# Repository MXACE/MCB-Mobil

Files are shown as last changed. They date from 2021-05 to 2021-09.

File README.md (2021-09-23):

# MCB-Mobil
A selfmade RC car with mecanuum wheels.

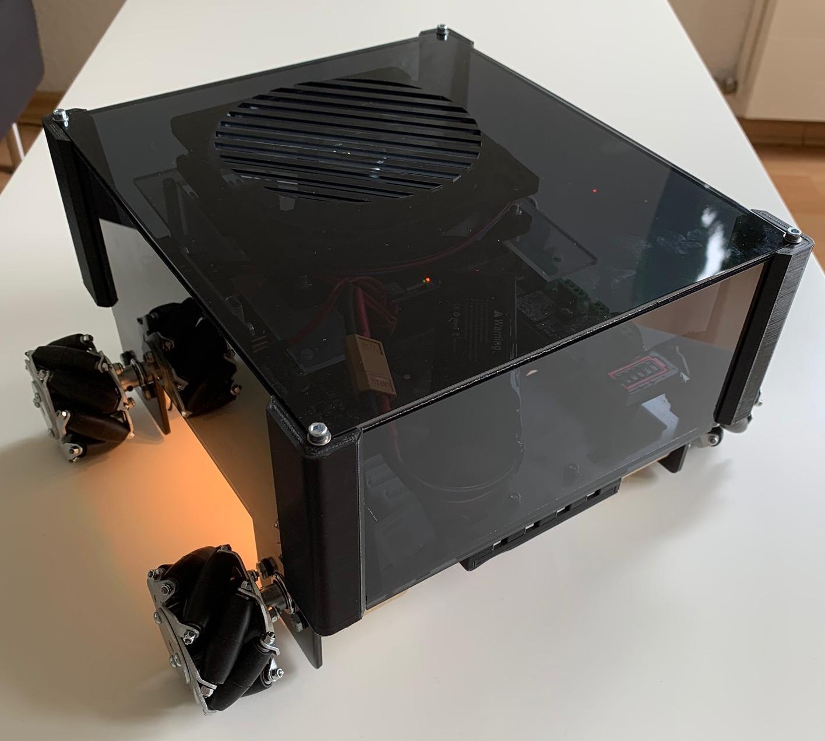
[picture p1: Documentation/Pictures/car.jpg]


## Important Notes
The Software written for the STM microcontroller is for the [STM32Workbench](https://www.st.com/en/development-tools/sw4stm32.html) IDE.
The Software written for the Arduino is made in [Arduino](https://www.arduino.cc/en/software)

The controller is on version 2.0. The old files of version 1.0 are not on this github.
See "Controller Changelog" or the documentation below for more information.

[First Documentation v1.0](https://github.com/MXACE/MCB-Mobil/tree/master/Documentation/MCB_Mobil_Doku_LarsPeter_MarcoStauber.pdf)

[Second Documentation (Controller v2.0)](https://github.com/MXACE/MCB-Mobil/tree/master/Documentation/Doku_controller.pdf)

## Controller Changelog
v2.0
- Added BMG250 Sensor.
- Removed OLED Connector.
- Added OLED Screen COM connector.
- Changed microcontroller from STM32F107VC to STM32F405RGT6.
- Removed connection for Lora Breakout Board.
- Added RN2483 Lora Module directly on PCB.
- Replaced 20pin JTAG conntector with 5 Pin SWD connector and TagConnect pads.
- Removed onboard STLINK and it's USB Connector.
- Added Powerswitch between Battery and USB.
- Several layout changes.

## Important Files:

Schematics of the Car, Controller and the Lora Breakoutboard can be found [here](https://github.com/MXACE/MCB-Mobil/tree/master/All_Schematics)

### Car:
- [PCB Files](https://github.com/MXACE/MCB-Mobil/tree/master/Car/CAD/v1.0/Chassisv1.0)
- [3D Printed Casing Parts (Scheinwerfer & Plexiglashalter)](https://github.com/MXACE/MCB-Mobil/tree/master/Car/3d%20modell/3dprint)
- [Software for STM32F107](https://github.com/MXACE/MCB-Mobil/tree/master/Car/SW)
- [Software for Arduino Nano](https://github.com/MXACE/MCB-Mobil/tree/master/Car/SW_ARD)
- [BOM](https://github.com/MXACE/MCB-Mobil/tree/master/Car/Assembly)

### Controller:
- [PCB Files](https://github.com/MXACE/MCB-Mobil/tree/master/Controller/PCB)
- [3D Printed Casing Parts](https://github.com/MXACE/MCB-Mobil/tree/master/Controller/Assembly)
- [Software for STM32F405](https://github.com/MXACE/MCB-Mobil/tree/master/Controller/SW)
- [BOM](https://github.com/MXACE/MCB-Mobil/tree/master/Controller/BOM)

### RN2483 Lora Breakout Module
- [PCB Files](https://github.com/MXACE/MCB-Mobil/tree/master/Funk/CAD/v1.0/PCB_Project)
- [BOM](https://github.com/MXACE/MCB-Mobil/tree/master/Funk/Assembly)

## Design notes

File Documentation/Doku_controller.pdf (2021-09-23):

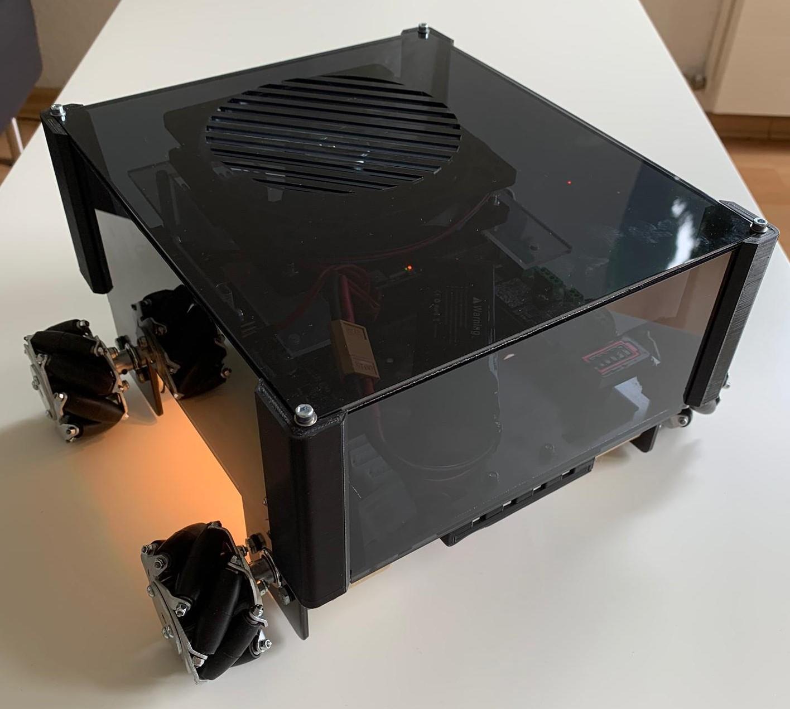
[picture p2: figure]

# MCB Mobil

Marco Stauber

Ben17A

## Inhaltsverzeichnis

## Abstract

Die erste Version des Kontrollers funktionierte nicht mehr und hatte viele Designfehler. Am einfachsten ging es mit einem neuem Design und einem neuem Print.
Das Ziel war es das bereits begonnene Projekt „MCB Mobil“ fertig zu stellen und ein zweites Fahrzeug für Herrn Malacarne zusammen zu bauen.

## Zusätzliche Infos

Alle Dateien für das Projekt können auf dem folgenden GitHub gefunden werden:

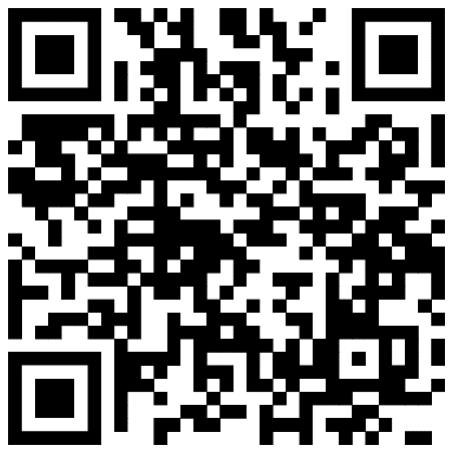
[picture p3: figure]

https://github.com/MXACE/MCB-Mobil

## Änderungen

Anstelle eines RN2483-Breakoutboard das ich selbst gemacht habe, befindet sich direkt ein solches Modul auf dem Print. Dieses ist zuständig für die Kommunikation mit dem Fahrzeug. Zur Sicherheit habe ich den Footprint des Breakoutboards trotzdem hinzugefügt, falls das Modul auf dem PCB nicht funktioniert.

Da das mit dem Bootloader nicht geklappt hat, konnte ich ihn ganz weg lassen. Somit sparte ich nicht nur Platz, sondern auch noch Geld und viele Bauteile wie ein zweiter Mikrokontroller oder ein USB Anschluss.

Die Joysticks befinden sich nun auf der gleichen Höhe vom Print. Ein Fehler den ich gemacht habe war, dass ich den linken Joystick nicht um 45° gedreht habe. Dies würde es vereinfachen das Fahrzeug zu steuern, da es mit den Mecannum Rädern andere Fahrtrichtungen hat.

Diese Räder besitzen Rollen die im 45° Winkel montiert wurden. Somit verändert es die Fahrtrichtung.
In der linken Abbildung sieht man die Fahrtrichtungen mit herkömmlichen Rädern.
In der rechten Abbildung sieht man die orangen Kräftevektoren der einzelnen Räder. Kombiniert man diese beliebig, kann man mit dem Fahrzeug in alle Richtungen fahren.

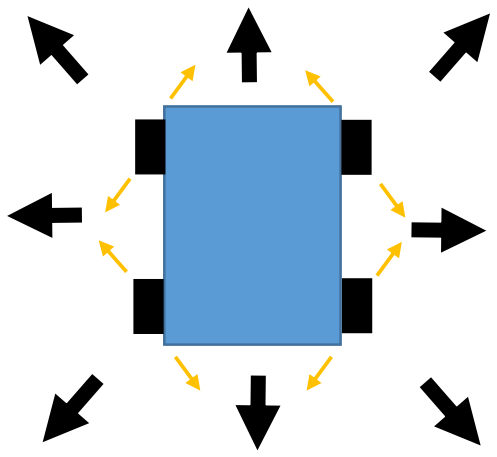
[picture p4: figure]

Neben den zusätzlichen Debug-LEDs gibt jetzt noch eine Schaltung für die Speisung. Ein PMOS stellt die Speisung der Batterie hochohmig, sobald sich eine Spannung am USB-Port befindet. Dies soll verhindern, dass die Batterie sich schnell entlädt.

Ein Achsensensor, der BMG250 von Bosch, sollte eine zweite Möglichkeit sein um das Fahrzeug zu steuern, indem man den Kontroller in die jeweilige Richtung kippt.

## Funktionen

Um das eine Problem mit den Joystick zu beheben, musst ich nur die XY Koordinaten davon um 45° drehen. Durch eine Anleitung auf YouTube konnte ich einfach herausfinden wie es funktioniert.

∝ = 45° → cos(∝) = sin(∝) =

√2
2

= √0.5 ≈ 0.707

x45 = x × cos(∝) − y × sin(∝) = x × √0.5 − y × √0.5

y45 = x × cos(∝) + y × sin(∝) = x × √0.5 + y × √0.5

Da der Sinus und der Cosinus aus der Math.h Library den ganzen Speicher füllen würden nahm ich anstelle von cos(45°) und sin(45°), 0.707 für die Rechnung.

Da mir die Zeit fehlte kam ich nicht weit beim Kommunikationsprotokoll zwischen dem Fahrzeug und dem Kontroller. Also war die Lösung: eine Kommunikation nur in eine Richtung. Der Kontroller schickt alle 0.5 Sekunden eine Nachricht mit allen Joystick Werten. Im Fall das eine Nachricht ausfallen sollte und das Fahrzeug 0.5 Sekunden lang keine Daten bekommt, bleibt es stehen. Der Kontroller muss daher einfach neugestartet werden. Das Fahrzeug wartet ein paar Sekunden und geht dann wieder in RX Modus. Gleichzeitig sieht man das an den LEDS um das Fahrzeug.

Der Bildschirm ist nun ein wenig überflüssig. Dieser zeigt nur noch an wann der Kontroller bereit ist für den Start und die Steuerung des Scheinwerfers.

## Probleme

Der Achsensensor hat mich sehr viel Zeit gekostet. Das Hautproblem war die Kommunikation mit dem Chip. Designt habe ich ihn für SPI. Nach nahezu endlosen neuprogrammieren und neu löten wurde es immer noch nichts. Als ich es mit einem STM Discovery und der Breakout Version des BMG250 über I2C versuchte ging es. Auf dem Kontroller wiederrum nicht, also hab ich das ganze sein gelassen.

Bei dem Aufsetzten der Unidirektionalen Kommunikation gab es auch ein Paar Fehler die aber auf der Priorität der Interrupts zurückzuführen war.

## Fazit

Nun im letzten Semester konnte ich mein Fahrzeug endlich fertig stellen. Das mit dem Achsensensor fand ich eine coole Idee, wurde aber nur anstrengend und hat mich zu viel Zeit gekostet. Für das ich gesamthaft Eineinhalb Jahre an diesem Projekt dran war, hat es mir sehr viel Freude bereitet. Es war nicht immer einfach daran zu arbeiten, da viele Abschlussprüfungen und sonst noch welche Dinge dazwischen kamen.

Das Fahrzeug fährt jetzt immerhin und es funktioniert grösstenteils. Es gäbe noch ein paar Verbesserungen, wie zum Beispiel eine Akkuschutzschaltung oder einen kleineren Print, die man bei der nächsten Version machen könnte.

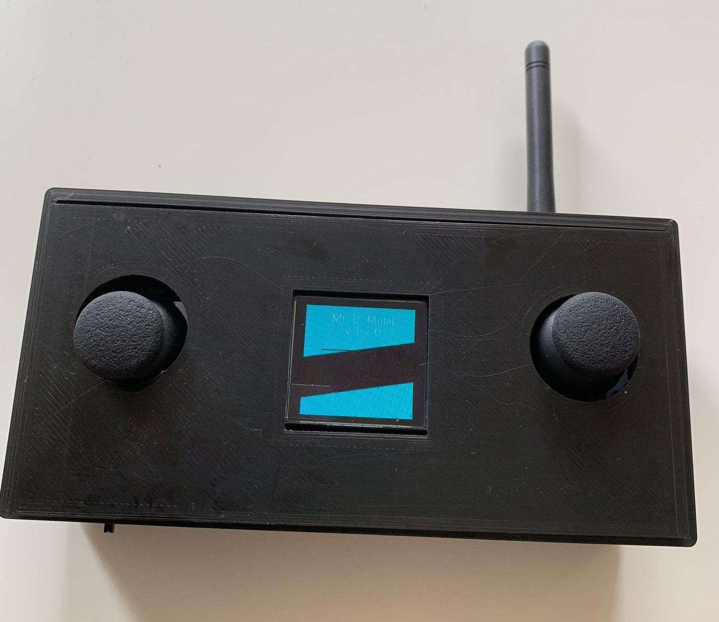
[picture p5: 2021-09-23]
Documentation/Pictures/Controller.jpg

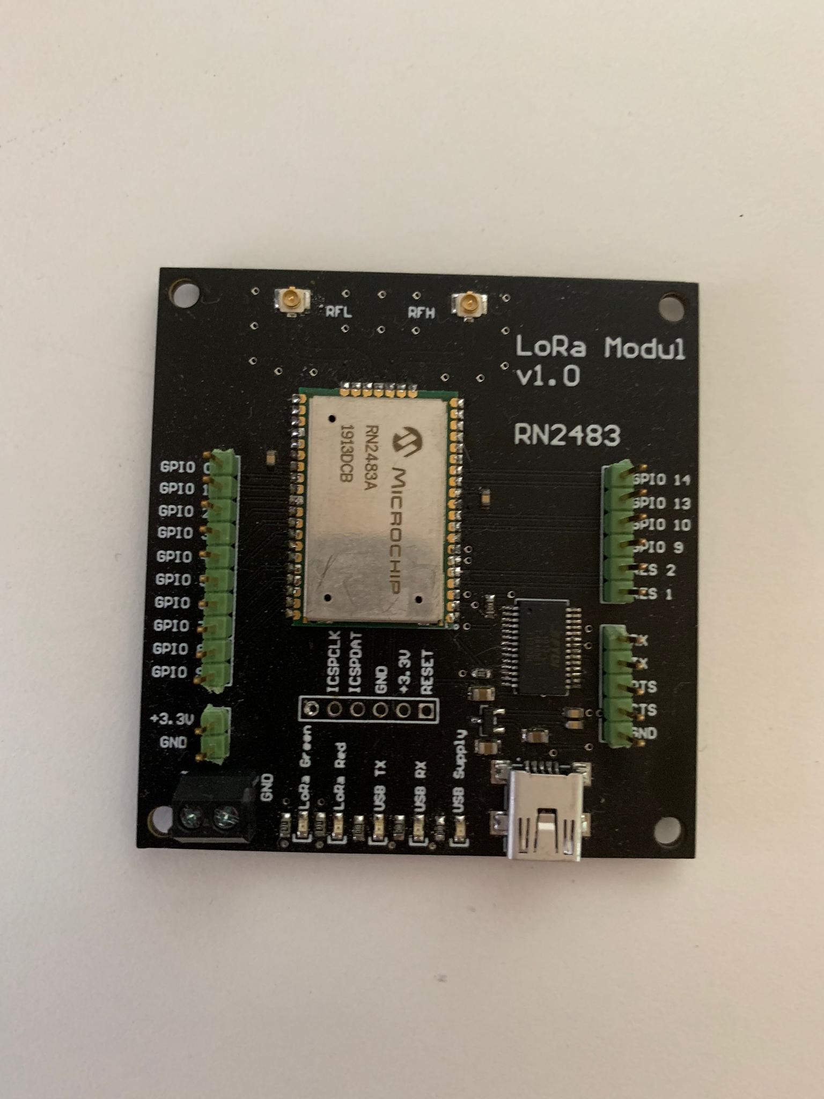
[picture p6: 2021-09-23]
Documentation/Pictures/LoraBreakout.jpg

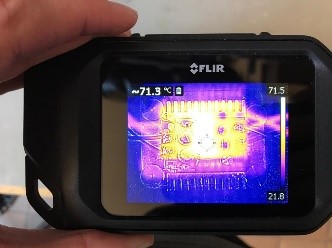
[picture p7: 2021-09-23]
Documentation/Pictures/Temperature_DCDC.jpg

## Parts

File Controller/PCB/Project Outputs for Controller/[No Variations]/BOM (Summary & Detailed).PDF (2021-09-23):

Designator | Description | Comment | Footprint | Quantity | Ma nuf No act te ure r | Su Su Su ppl ppl ppl ier ier ier 1 2 3 | Su Su Su ppl ppl ppl ier ier ier 1 2 3 Par Par Par t t t Nu Nu Nu mb mb mb er er er | Ma nuf act SMS-ure r Lab Par Part t Num ber Nu mb er | Value | Center-X(mm) | Center-Y(mm) | Layer | Assembly Technology | Rotation
| | LoRa Modul | LoRA | | 1 | | | | | 73.51 | 30.811 | Bottom | | 270
C1 | capacitor | 22 pF | CAP_0603i_1608m -N | | 1 | | | | | 90.369 | 21.535 | Top | | 180
C2 | capacitor | 22 pF | CAP_0603i_1608m -N | | 1 | | | | | 93.8 | 18.682 | Top | | 270
C3 | capacitor | 100nF | CAP_0603i_1608m -N | | 1 | | | | | 126.3 | 10.6 | Top | | 0
C4 | capacitor | 100nF | CAP_0603i_1608m -N | | 1 | | | | | 94.226 | 13.684 | Top | | 0
C5 | | Capacitor_0805 | 10uF_0805_Chip2Pi nSM127P600-8N | | 1 | | | | | 131.35 | 56.691 | Top | | 270
C6 | capacitor | 1 uF | CAP_0805i_2012m -N | | 1 | | | | | 80.2 | 59.882 | Top | | 90
C7 | | Capacitor_0603 | C_0603_Chip2PinS M127P600-8N | | 1 | | | | | 111.35 | 64.35 | Top | | 180
C8 | capacitor | 1 uF | CAP_0805i_2012m -N | | 1 | | | | | 70.9 | 60.103 | Top | | 270
C9 | | Capacitor_0603 | C_0603_Chip2PinS M127P600-8N | | 1 | | | | | 118.2 | 56.7 | Top | | 90
C10 | | Capacitor_0603 | C_0603_Chip2PinS M127P600-8N | | 1 | | | | | 59 | 47.585 | Top | | 180
C11 | | Capacitor_0603 | C_0603_Chip2PinS M127P600-8N | | 1 | | | | | 119.9 | 56.7 | Top | | 90
C12 | | Capacitor_0603 | C_0603_Chip2PinS M127P600-8N | | 1 | | | | | 133.35 | 56.691 | Top | | 90
C13 | | Capacitor_0603 | C_0603_Chip2PinS M127P600-8N | | 1 | | | | | 121.55 | 56.7 | Top | | 90
C14 | capacitor | 100nF | CAP_0603i_1608m -L | | 1 | | | | | 58.558 | 54.86 | Top | | 180
C15 | capacitor | 10 uF | CAP_0805i_2012m -N | | 1 | | | | | 55.568 | 61.238 | Top | | 270
C16 | capacitor | 100nF | CAP_0603i_1608m -L | | 1 | | | | | 51.653 | 58.8 | Top | | 270
C17 | capacitor | 22 pF | CAP_0603i_1608m -N | | 1 | | | | | 82.362 | 36.166 | Top | | 90
C18 | capacitor | 0.1 uF | CAP_0603i_1608m -N | | 1 | | | | | 81.583 | 31.445 | Top | | 270
C19 | capacitor | 0.1 uF | CAP_0603i_1608m -N | | 1 | | | | | 70.42 | 46.456 | Top | | 180
C20 | capacitor | 22 pF | CAP_0603i_1608m -N | | 1 | | | | | 78.658 | 31.453 | Top | | 90
C21 | capacitor | 0.1 uF | CAP_0603i_1608m -N | | 1 | | | | | 70 | 25.306 | Top | | 0
C22 | capacitor | 0.1 uF | CAP_0603i_1608m -N | | 1 | | | | | 51.653 | 28.756 | Top | | 90
C23 | capacitor | 0.1 uF | CAP_0603i_1608m -N | | 1 | | | | | 59 | 45.85 | Top | | 180
C24 | capacitor | 0.1 uF | CAP_0603i_1608m -N | | 1 | | | | | 79.63 | 39.112 | Top | | 0
C25 | capacitor | 0.1 uF | CAP_0603i_1608m -N | | 1 | | | | | 78 | 40.624 | Top | | 180
C26 | capacitor | 0.1 uF | CAP_0603i_1608m -N | | 1 | | | | | 78 | 42.306 | Top | | 0
C27 | capacitor | 10 uF | CAP_0805i_2012m -N | | 1 | | | | | 86.908 | 49.15 | Top | | 180
CR1 | | STM32F103C8T6 | LQFP-48 | | 1 | | | | STM32F 103C8T 6 | 103.582 | 16.044 | Top | | 0
D1 | LED; SMD; 0603; grün; 35mcd; 1.6x0.8x0.55mm; 130Â°; 2Ã·2.V; 20mA | Grün | *0603 | | 1 | | | | | 120.963 | 2.6 | Top | | 90
D2 | LED; SMD; 0603; orange; 45-90mcd; 1.6x0.8x0.55mm; 130Â°; 2Ã·2.4V; 20mA | Orange | *0603 | | 1 | | | | | 118.882 | 2.6 | Top | | 90
D3 | LED; SMD; 0603; grün; 35mcd; 1.6x0.8x0.55mm; 130Â°; 2Ã·2.V; 20mA | Grün | *0603 | | 1 | | | | | 80.2 | 67.704 | Top | | 270
D4 | | BAT54T1G | BAT54T1G_SODFL3 71X135-2N | | 1 | | | | | 105.985 | 61.975 | Top | | 180
D5 | LED; SMD; 0603; grün; 35mcd; 1.6x0.8x0.55mm; 130Â°; 2Ã·2.V; 20mA | Grün | *0603 | | 1 | | | | | 51.051 | 66.882 | Top | | 270
D6 | LED; SMD; 0603; orange; 45-90mcd; 1.6x0.8x0.55mm; 130Â°; 2Ã·2.4V; 20mA | Orange | *0603 | | 1 | | | | | 53.178 | 66.882 | Top | | 270
D7 | | 1N4148 | 1N4148_SODFL127P 600-8N | | 1 | | | | | 127.35 | 56.691 | Top | | 90
D8 | | 1N4148 | 1N4148_SODFL127P 600-8N | | 1 | | | | | 125.35 | 56.691 | Top | | 270
D9 | LED; SMD; 0603; grün; 35mcd; 1.6x0.8x0.55mm; 130Â°; 2Ã·2.V; 20mA | Grün | *0603 | | 1 | | | | | 24.07 | 14.9 | Top | | 270
F1 | | Fuse | FUSE-3586KTR | | 1 | | | | | 19.02 | 8.95 | Top | | 0
IC1 | USB-to-UART 1-CH 256byte FIFO 5V 28-Pin SSOP Tube | FT232RL-TUBE | *SSOP28-LD | | 1 | | | | | 50.678 | 50.193 | Top | | 0
J1 | Mini AB, USB 2.0, 1 A, Right Angle, Surface Mount _SMT_, USB Receptacle | UJ2-MABH-4-SMT | *CUI_UJ2-MABH-4-SMT_UJ2-MABH-4-SMT(Primary) | | 1 | | | | | 129.3 | 5.16 | Top | | 0
J2 | Mini AB, USB 2.0, 1 A, Right Angle, Surface Mount _SMT_, USB Receptacle | UJ2-MABH-4-SMT | *CUI_UJ2-MABH-4-SMT_UJ2-MABH-4-SMT(Primary) | | 1 | | | | | 63.48 | 64.87 | Top | | 180
J3 | | Joystick | Joystick | | 1 | | | | | 21.99 | 39.004 | Top | | 0
J4 | | Joystick | Joystick | | 1 | | | | | 128.01 | 39 | Top | | 180
L1 | | Inductor_0805 | 0805_INDC2012X12 N | | 1 | | | | | 103.35 | 64.975 | Top | | 270
L2 | Inductor | Inductor | Murata Inductor 2900 sch | | 1 | | | | | 79.923 | 46.85 | Top | | 90
P1 | Header, 4-Pin | Header 4 | HDR1X4 | | 1 | | | | | 114.421 | 21.533 | Top | | 180
P2 | Header, 5-Pin | SWIM | HDR1X5 | | 1 | | | | | 102.042 | 32.254 | Top | | 0
P3 | Header, 5-Pin | SWD | HDR1X5 | | 1 | | | | | 122.582 | 15.895 | Top | | 90
P6 | Single Pad or Testpoint | ON-OFF | MotConnector | | 1 | | | | | 14.8 | 2.9 | Top | | 0
P7 | Connector; IDC, Male Header, Thru-Hole; 20 Position; Vertical; Pitch 2.54mm; B | IDC-20 | IDC-20 | | 1 | | | | | 24.7 | 62.96 | Top | | 0
P8 | Single Pad or Testpoint | Batterie | MotConnector | | 1 | | | | | 26.07 | 2.9 | Top | | 0
R1 | Resistor | 1000 | RES_0603i_1608m -N | | 1 | | | | | 120.963 | 6.6 | Top | | 90
R2 | Resistor | 1000 | RES_0603i_1608m -N | | 1 | | | | | 118.882 | 6.6 | Top | | 270
R3 | Resistor | 100K | RES_0603i_1608m -N | | 1 | | | | | 96.9 | 10.4 | Top | | 270
R4 | Resistor | 100K | RES_0603i_1608m -N | | 1 | | | | | 98.576 | 10.374 | Top | | 90
R5 | Resistor | 390 | RES_0603i_1608m -N | | 1 | | | | | 90.369 | 15.657 | Top | | 0
R6 | Resistor | 10K | RES_0603i_1608m -N | | 1 | | | | | 102.218 | 34.59 | Top | | 0
R7 | Resistor | 10K | RES_0603i_1608m -N | | 1 | | | | | 104.332 | 8.454 | Top | | 90
R8 | Resistor | 10K | RES_0603i_1608m -N | | 1 | | | | | 94.226 | 15.397 | Top | | 180
R9 | Resistor | 220 | RES_0603i_1608m -N | | 1 | | | | | 101.888 | 24.814 | Top | | 270
R10 | Resistor | 220 | RES_0603i_1608m -N | | 1 | | | | | 104.83 | 24.814 | Top | | 270
R11 | Resistor | 220 | RES_0603i_1608m -N | | 1 | | | | | 99.463 | 28.544 | Top | | 270
R12 | Resistor | 100 | RES_0603i_1608m -N | | 1 | | | | | 114.453 | 13.355 | Top | | 180
R13 | Resistor | 22 | RES_0603i_1608m -N | | 1 | | | | | 101.888 | 28.564 | Top | | 270
R14 | Resistor | 22 | RES_0603i_1608m -N | | 1 | | | | | 104.776 | 28.56 | Top | | 270
R15 | Resistor | 22 | RES_0603i_1608m -N | | 1 | | | | | 118.103 | 13.355 | Top | | 180
R16 | Resistor | 22 | RES_0603i_1608m -N | | 1 | | | | | 118.103 | 15.895 | Top | | 180
R17 | Resistor | 22 | RES_0603i_1608m -N | | 1 | | | | | 118.103 | 18.435 | Top | | 180
R18 | Resistor | 1K | RES_0603i_1608m -N | | 1 | | | | | 80.2 | 63.742 | Top | | 90
R19 | | Resistor_0603 | R_0603_Chip2PinS M127P600-8N | | 1 | | | | | 111.35 | 62.735 | Top | | 0
R20 | | Resistor_0603 | R_0603_Chip2PinS M127P600-8N | | 1 | | | | | 111.35 | 65.925 | Top | | 180
R21 | Resistor | 1000 | RES_0603i_1608m -N | | 1 | | | | | 51.051 | 62.882 | Top | | 90
R22 | Resistor | 1000 | RES_0603i_1608m -N | | 1 | | | | | 53.178 | 62.882 | Top | | 90
R23 | Resistor | 1K | RES_0603i_1608m -N | | 1 | | | | | 46.453 | 43.851 | Top | | 270
R24 | Resistor | 1K | RES_0603i_1608m -N | | 1 | | | | | 49.079 | 43.851 | Top | | 270
R25 | | Resistor_0603 | R_0603_Chip2PinS M127P600-8N | | 1 | | | | | 129.35 | 56.691 | Top | | 90
R26 | | Resistor_0603 | R_0603_Chip2PinS M127P600-8N | | 1 | | | | | 123.2 | 56.7 | Top | | 90
R27 | Resistor | Res | RES_0603i_1608m -N | | 1 | | | | | 76.11 | 31.598 | Top | | 90
R28 | Resistor | 390 | RES_0603i_1608m -N | | 1 | | | | | 76.86 | 36.206 | Top | | 270
R29 | Resistor | 10K | RES_0603i_1608m -N | | 1 | | | | | 20.8 | 14.9 | Top | | 90
R30 | Resistor | 10K | RES_0603i_1608m -N | | 1 | | | | | 28.51 | 55.925 | Top | | 270
R31 | Resistor | 10K | RES_0603i_1608m -N | | 1 | | | | | 25.97 | 55.925 | Top | | 270
R32 | Resistor | 10K | RES_0603i_1608m -N | | 1 | | | | | 21 | 55.925 | Top | | 270
R33 | Resistor | 10K | RES_0603i_1608m -N | | 1 | | | | | 56.9 | 26.208 | Top | | 90
R34 | Resistor | 10K | RES_0603i_1608m -N | | 1 | | | | | 18.4 | 55.925 | Top | | 270
R35 | Resistor | 10K | RES_0603i_1608m -N | | 1 | | | | | 33.59 | 55.925 | Top | | 90
R36 | Resistor | 10K | RES_0603i_1608m -N | | 1 | | | | | 15.9 | 55.925 | Top | | 270
R37 | Resistor | 10K | RES_0603i_1608m -N | | 1 | | | | | 36.13 | 55.925 | Top | | 90
S1 | Switch | SW PB | B3SL-1002P | | 1 | | | | | 78.86 | 26.218 | Top | | 180
U1 | | OLED_Driver | FAN5331S_SOT2312 7P600-8N | | 1 | | | | | 107.35 | 64.975 | Top | | 180
U2 | 3.3V Voltage Regulator | Part Number: AP2120N-3.3TRG1 | SOT-23-M | | 1 | | | | Value | 74.6 | 60.1 | Top | | 270
U3 | STM32 Series 32-bit 256 kB Flash 64 kB RAM ARM Based Microcontroller -LQFP-100 | STM32F107VCT6 | *QFP50P1600X1600 X160-100N | | 1 | | | | | 64.71 | 35.456 | Top | | 180
U4 | Ldo.Vreg Pos 3, 3v 1a Sot223 | AZ1117EH-3.3TRG1 | *SOT230P700X180-4N | | 1 | | | | | 15.11 | 16.49 | Top | | 0
X1 | | Molex_FlatFlex-to-Board | MOLEX_FTB_30 | | 1 | | | | | 126.75 | 62.47 | Top | | 180
Y1 | Industrial Ceramic Resonator | XTAL3 | TSX-3225 2*2.5 | | 1 | | | | | 90.619 | 18.657 | Top | | 0
Y2 | Industrial Ceramic Resonator | XTAL3 | TSX-3225 2*2.5 | | 1 | | | | | 79.485 | 35.956 | Top | | 270

Assembly Technology | Comment | Description | Designator | Footprint | LibRef | Quantity | SMS-Lab Part Number | Supplier 1 Part Number | Supplier 2 Part Number | Supplier 3 Part Number | Manufacturer | Manufacturer Part Number | Supplier 1 | Supplier 2 | Supplier 3
| LoRa Modul | | | LoRA | LoRa Modul | | 1
| 22 pF | capacitor | C1 | CAP_0603i_1 608m -N | Cap | | 1
| 22 pF | capacitor | C2 | CAP_0603i_1 608m -N | Cap | | 1
| 100nF | capacitor | C3 | CAP_0603i_1 608m -N | Cap | | 1
| 100nF | capacitor | C4 | CAP_0603i_1 608m -N | Cap | | 1
| Capacitor_0805 | | C5 | 10uF_0805_C hip2PinSM12 7P600-8N | Capacitor_0805 | | 1
| 1 uF | capacitor | C6 | CAP_0805i_2 012m -N | Cap | | 1
| Capacitor_0603 | | C7 | C_0603_Chip 2PinSM127P 600-8N | Capacitor_0603 | | 1
| 1 uF | capacitor | C8 | CAP_0805i_2 012m -N | Cap | | 1
| Capacitor_0603 | | C9 | C_0603_Chip 2PinSM127P 600-8N | Capacitor_0603 | | 1
| Capacitor_0603 | | C10 | C_0603_Chip 2PinSM127P 600-8N | Capacitor_0603 | | 1
| Capacitor_0603 | | C11 | C_0603_Chip 2PinSM127P 600-8N | Capacitor_0603 | | 1
| Capacitor_0603 | | C12 | C_0603_Chip 2PinSM127P 600-8N | Capacitor_0603 | | 1
| Capacitor_0603 | | C13 | C_0603_Chip 2PinSM127P 600-8N | Capacitor_0603 | | 1
| 100nF | capacitor | C14 | CAP_0603i_1 608m -L | Cap | | 1
| 10 uF | capacitor | C15 | CAP_0805i_2 012m -N | Cap | | 1
| 100nF | capacitor | C16 | CAP_0603i_1 608m -L | Cap | | 1
| 22 pF | capacitor | C17 | CAP_0603i_1 608m -N | Cap | | 1
| 0.1 uF | capacitor | C18 | CAP_0603i_1 608m -N | Cap | | 1
| 0.1 uF | capacitor | C19 | CAP_0603i_1 608m -N | Cap | | 1
| 22 pF | capacitor | C20 | CAP_0603i_1 608m -N | Cap | | 1
| 0.1 uF | capacitor | C21 | CAP_0603i_1 608m -N | Cap | | 1
| 0.1 uF | capacitor | C22 | CAP_0603i_1 608m -N | Cap | | 1
| 0.1 uF | capacitor | C23 | CAP_0603i_1 608m -N | Cap | | 1
| 0.1 uF | capacitor | C24 | CAP_0603i_1 608m -N | Cap | | 1
| 0.1 uF | capacitor | C25 | CAP_0603i_1 608m -N | Cap | | 1
| 0.1 uF | capacitor | C26 | CAP_0603i_1 608m -N | Cap | | 1
| 10 uF | capacitor | C27 | CAP_0805i_2 012m -N | Cap | | 1
| STM32F103C8T6 | | CR1 | LQFP-48 | STM32F103C8T6 | | 1
| Grün | LED; SMD; 0603; grün; 35mcd; 1.6x0.8x0.55mm; 130Â°; 2Ã·2.V; 20mA | D1 | *0603 | LTST-C191KGKT | | 1
| Orange | LED; SMD; 0603; orange; 45-90mcd; 1.6x0.8x0.55mm; 130Â°; 2Ã·2.4V; 20mA | D2 | *0603 | LTST-C191KFKT | | 1
| Grün | LED; SMD; 0603; grün; 35mcd; 1.6x0.8x0.55mm; 130Â°; 2Ã·2.V; 20mA | D3 | *0603 | LTST-C191KGKT | | 1
| BAT54T1G | | D4 | BAT54T1G_S ODFL371X13 5-2N | BAT54T1G | | 1
| Grün | LED; SMD; 0603; grün; 35mcd; 1.6x0.8x0.55mm; 130Â°; 2Ã·2.V; 20mA | D5 | *0603 | LTST-C191KGKT | | 1
| Orange | LED; SMD; 0603; orange; 45-90mcd; 1.6x0.8x0.55mm; 130Â°; 2Ã·2.4V; 20mA | D6 | *0603 | LTST-C191KFKT | | 1
| 1N4148 | | D7 | 1N4148_SOD FL127P600-8N | 1N4148 | | 1
| 1N4148 | | D8 | 1N4148_SOD FL127P600-8N | 1N4148 | | 1
| Grün | LED; SMD; 0603; grün; 35mcd; 1.6x0.8x0.55mm; 130Â°; 2Ã·2.V; 20mA | D9 | *0603 | LTST-C191KGKT | | 1
| Fuse | | F1 | FUSE-3586KTR | Fuse | | 1
| FT232RL-TUBE | USB-to-UART 1-CH 256byte FIFO 5V 28-Pin SSOP Tube | IC1 | *SSOP28-LD | FT232RL-TUBE | | 1
| UJ2-MABH-4-SMT | Mini AB, USB 2.0, 1 A, Right Angle, Surface Mount _SMT_, USB Receptacle | J1 | *CUI_UJ2-MABH-4-SMT_UJ2-MABH-4-SMT(Primary ) | UJ2-MABH-4-SMT | | 1
| UJ2-MABH-4-SMT | Mini AB, USB 2.0, 1 A, Right Angle, Surface Mount _SMT_, USB Receptacle | J2 | *CUI_UJ2-MABH-4-SMT_UJ2-MABH-4-SMT(Primary ) | UJ2-MABH-4-SMT | | 1
| Joystick | | J3 | Joystick | Joystick | | 1
| Joystick | | J4 | Joystick | Joystick | | 1
| Inductor_0805 | | L1 | 0805_INDC20 12X12N | Inductor_0805 | | 1
| Inductor | Inductor | L2 | Murata Inductor 2900 sch | Inductor | | 1
| Header 4 | Header, 4-Pin | P1 | HDR1X4 | Header 4 | | 1
| SWIM | Header, 5-Pin | P2 | HDR1X5 | Header 5 | | 1
| SWD | Header, 5-Pin | P3 | HDR1X5 | Header 5 | | 1
| ON-OFF | Single Pad or Testpoint | P6 | MotConnect or | Pad, double | | 1
| IDC-20 | Connector; IDC, Male Header, Thru-Hole; 20 Position; Vertical; Pitch 2.54mm; B | P7 | IDC-20 | IDC-20 | | 1
| Batterie | Single Pad or Testpoint | P8 | MotConnect or | Pad, double | | 1
| 1000 | Resistor | R1 | RES_0603i_1 608m -N | Res | | 1
| 1000 | Resistor | R2 | RES_0603i_1 608m -N | Res | | 1
| 100K | Resistor | R3 | RES_0603i_1 608m -N | Res | | 1
| 100K | Resistor | R4 | RES_0603i_1 608m -N | Res | | 1
| 390 | Resistor | R5 | RES_0603i_1 608m -N | Res | | 1
| 10K | Resistor | R6 | RES_0603i_1 608m -N | Res | | 1
| 10K | Resistor | R7 | RES_0603i_1 608m -N | Res | | 1
| 10K | Resistor | R8 | RES_0603i_1 608m -N | Res | | 1
| 220 | Resistor | R9 | RES_0603i_1 608m -N | Res | | 1
| 220 | Resistor | R10 | RES_0603i_1 608m -N | Res | | 1
| 220 | Resistor | R11 | RES_0603i_1 608m -N | Res | | 1
| 100 | Resistor | R12 | RES_0603i_1 608m -N | Res | | 1
| 22 | Resistor | R13 | RES_0603i_1 608m -N | Res | | 1
| 22 | Resistor | R14 | RES_0603i_1 608m -N | Res | | 1
| 22 | Resistor | R15 | RES_0603i_1 608m -N | Res | | 1
| 22 | Resistor | R16 | RES_0603i_1 608m -N | Res | | 1
| 22 | Resistor | R17 | RES_0603i_1 608m -N | Res | | 1
| 1K | Resistor | R18 | RES_0603i_1 608m -N | Res | | 1
| Resistor_0603 | | R19 | R_0603_Chip 2PinSM127P 600-8N | Resistor_0603 | | 1
| Resistor_0603 | | R20 | R_0603_Chip 2PinSM127P 600-8N | Resistor_0603 | | 1
| 1000 | Resistor | R21 | RES_0603i_1 608m -N | Res | | 1
| 1000 | Resistor | R22 | RES_0603i_1 608m -N | Res | | 1
| 1K | Resistor | R23 | RES_0603i_1 608m -N | Res | | 1
| 1K | Resistor | R24 | RES_0603i_1 608m -N | Res | | 1
| Resistor_0603 | | R25 | R_0603_Chip 2PinSM127P 600-8N | Resistor_0603 | | 1
| Resistor_0603 | | R26 | R_0603_Chip 2PinSM127P 600-8N | Resistor_0603 | | 1
| Res | Resistor | R27 | RES_0603i_1 608m -N | Res | | 1
| 390 | Resistor | R28 | RES_0603i_1 608m -N | Res | | 1
| 10K | Resistor | R29 | RES_0603i_1 608m -N | Res | | 1
| 10K | Resistor | R30 | RES_0603i_1 608m -N | Res | | 1
| 10K | Resistor | R31 | RES_0603i_1 608m -N | Res | | 1
| 10K | Resistor | R32 | RES_0603i_1 608m -N | Res | | 1
| 10K | Resistor | R33 | RES_0603i_1 608m -N | Res | | 1
| 10K | Resistor | R34 | RES_0603i_1 608m -N | Res | | 1
| 10K | Resistor | R35 | RES_0603i_1 608m -N | Res | | 1
| 10K | Resistor | R36 | RES_0603i_1 608m -N | Res | | 1
| 10K | Resistor | R37 | RES_0603i_1 608m -N | Res | | 1
| SW PB | Switch | S1 | B3SL-1002P | SW PB | | 1
| OLED_Driver | | U1 | FAN5331S_S OT23127P600-8N | OLED_Driver | | 1
| Part Number: AP2120N-3.3TRG1 | 3.3V Voltage Regulator | U2 | SOT-23-M | AP2120N-3.3TRG1 | | 1
| STM32F107VCT6 | STM32 Series 32-bit 256 kB Flash 64 kB RAM ARM Based Microcontroller -LQFP-100 | U3 | *QFP50P160 0X1600X160-100N | STM32F107VCT6 | | 1
| AZ1117EH-3.3TRG1 | Ldo.Vreg Pos 3, 3v 1a Sot223 | U4 | *SOT230P700 X180-4N | AZ1117EH-3.3TRG1 | | 1
| Molex_FlatFlex-to-Board | | X1 | MOLEX_FTB_ 30 | Molex_FlatFlex-to-Board | | 1
| XTAL3 | Industrial Ceramic Resonator | Y1 | TSX-3225 2*2.5 | XTAL3 | | 1
| XTAL3 | Industrial Ceramic Resonator | Y2 | TSX-3225 2*2.5 | XTAL3 | | 1

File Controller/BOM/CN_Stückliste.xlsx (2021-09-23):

 | Name | Desc | Partnumber | amount | price/p |  | total
Digikey | RN2483 | LoRa Modul | RN2483A-I/RM105-ND | 1 | CHF 11.65 |  | CHF 11.65
 | BMG250 | Gyroscope | 828-1065-1-ND | 1 | CHF 3.20 |  | CHF 3.20
 | USB4085-GF-A | USB C | 2073-USB4085-GF-ACT-ND | 1 | CHF 1.22 |  | CHF 1.22
 | RECE.20279.001E.01 | U.FL | 931-1107-1-ND | 1 | CHF 0.66 |  | CHF 0.66
 |  |  |  |  |  |  | CHF 0.00
 |  |  |  |  |  |  | CHF 0.00
 |  |  |  |  |  |  | CHF 0.00
 |  |  |  |  |  |  | CHF 0.00
 |  |  |  |  |  |  | CHF 0.00
 |  |  |  |  |  |  | CHF 0.00
 |  |  |  |  |  |  | CHF 0.00
 |  |  |  |  |  |  | CHF 0.00
 |  |  |  |  |  |  | CHF 0.00
 |  |  |  |  |  |  | CHF 0.00
 |  |  |  |  |  |  | CHF 0.00
 |  |  |  |  |  |  | CHF 0.00 | CHF 16.73
 |  |  |  |  |  | b/e
JLC | M24C02-WMN6TP | EEPROM, 2k (256x8) | C7562 | 1 | $0.09 | b | $0.09
 | STM32F730R8T6 | uC | C478453 | 1 | $2.69 | e | $2.69
 | UZ1084G-3.3V-TN3-R | 3.3V | C84897 | 1 | $0.28 | e | $0.28
 | LTST-C190GKT | led grün | C125093 |  |  |  | $0.00
 | LTST-C190KGKT | led rot | C125094 |  |  |  | $0.00
 |  |  |  |  |  |  | $0.00
 |  |  |  |  |  |  | $0.00
 |  |  |  |  |  |  | $0.00
 |  |  |  |  |  |  | $0.00
 |  |  |  |  |  |  | $0.00
 |  |  |  |  |  |  | $0.00
 |  |  |  |  |  |  | $0.00
 |  |  |  |  |  |  | $0.00
 |  |  |  |  |  |  | $0.00
 |  |  |  |  |  |  | $0.00
 |  |  |  |  |  |  | $0.00
 |  |  |  |  |  |  | $0.00
 |  |  |  |  |  |  | $0.00
 |  |  |  |  |  |  | $0.00
 |  |  |  |  |  |  | $0.00
 |  |  |  |  |  |  | $0.00
 |  |  |  |  |  |  | $0.00
 |  |  |  |  |  |  | $0.00
 |  |  |  |  |  |  | $0.00
 |  |  |  |  |  |  | $0.00 | $3.06

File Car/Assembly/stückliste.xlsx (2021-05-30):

POS | Name | Wert | Datenblatt | Digikeylink | Lieferant | Preis | Anzahl |  | Bestellt
SI7615ADN-T1-GE3CT-ND | SI7615ADN | P-Mosfet | http://www.vishay.com/docs/62667/si7615adn.pdf | https://www.digikey.ch/product-detail/de/vishay-siliconix/SI7615ADN-T1-GE3/SI7615ADN-T1-GE3CT-ND/3458170 | DigiKey | CHF 0.72 | 1 |  | 1 | CHF 0.72
MMBT3904-FDICT-ND | MMBT3904-7-F | Transistor | https://www.diodes.com/assets/Datasheets/ds30036.pdf | https://www.digikey.ch/product-detail/de/diodes-incorporated/MMBT3904-7-F/MMBT3904-FDICT-ND/815727 | DigiKey | CHF 0.12 | 1 |  |  | CHF 0.12
STM32F107VCT6 | STM32F107VCT6 | uC | https://www.st.com/content/ccc/resource/technical/document/datasheet/e4/f3/1a/89/5a/02/46/ae/CD00220364.pdf/files/CD00220364.pdf/jcr:content/translations/en.C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 | https://www.digikey.ch/product-detail/de/stmicroelectronics/STM32F107VCT6/497-8913-ND/2074107 | DigiKey | CHF 9.27 | 1 |  |  | CHF 9.27
296-28916-5-ND | DRV8840PWP | Motordriver | http://www.ti.com/lit/ds/symlink/drv8840.pdf | https://www.digikey.ch/product-detail/de/texas-instruments/DRV8840PWP/296-28916-5-ND/2676776 | DigiKey | CHF 4.30 | 4 |  |  | CHF 17.20
AZ1117EH-3.3TRG1DICT-ND | AZ1117EH-3.3TRG1 | 3.3V | https://www.diodes.com/assets/Datasheets/AZ1117E.pdf | https://www.digikey.ch/product-detail/de/diodes-incorporated/AZ1117EH-3.3TRG1/AZ1117EH-3.3TRG1DICT-ND/5001336 | DigiKey | CHF 0.43 | 1 |  |  | CHF 0.43
1276-1066-1-ND | CL21B105KAFNNNE | 1uF | http://www.samsungsem.com/kr/support/product-search/mlcc/__icsFiles/afieldfile/2019/06/18/CL21B105KAFNNNE-19.pdf | https://www.digikey.ch/product-detail/de/samsung-electro-mechanics/CL21B105KAFNNNE/1276-1066-1-ND/3889152 | DigiKey | CHF 0.08 | 1 |  |  | CHF 0.08
3314J-501ECT-ND | 3314J-1-501E | 500Ω | https://www.bourns.com/docs/Product-Datasheets/3314.pdf | https://www.digikey.ch/product-detail/de/bourns-inc/3314J-1-501E/3314J-501ECT-ND/86513 | DigiKey | CHF 2.16 | 1 |  |  | CHF 2.16
SER4211CT-ND | TSX-3225 25.0000MF10P-C0 | 25MHz | https://support.epson.biz/td/api/doc_check.php?dl=brief_TSX-3225&lang=en | https://www.digikey.ch/products/de?keywords=SER4211CT-ND | DigiKey | CHF 0.36 | 1 |  |  | CHF 0.36
399-7874-1-ND | CAP CER 22PF 100V C0G/NP0 0603 | 22pF | https://content.kemet.com/datasheets/KEM_C1003_C0G_SMD.pdf | https://www.digikey.ch/product-detail/de/kemet/C0603C220J1GACTU/399-7874-1-ND/3471597 | DigiKey | CHF 0.10 | 4 |  |  | CHF 0.40
SW1064CT-ND | B3SL-1002P | Taster | https://omronfs.omron.com/en_US/ecb/products/pdf/en-b3sl.pdf | https://www.digikey.ch/product-detail/de/omron-electronics-inc-emc-div/B3SL-1002P/SW1064CT-ND/2002628 | DigiKey | CHF 0.87 | 1 |  |  | CHF 0.87
MCS1632R050FERCT-ND | MCS1632R050FER | 50mΩ | https://www.ohmite.com/assets/docs/res_mcs.pdf?r=false | https://www.digikey.ch/product-detail/de/ohmite/MCS1632R050FER/MCS1632R050FERCT-ND/2003877 | DigiKey | CHF 0.67 | 6 |  |  | CHF 4.02
296-35964-1-ND | ULN2803ADWRG4 | LED treiber CA | http://www.ti.com/lit/ds/symlink/uln2803a.pdf | https://www.digikey.ch/product-detail/de/texas-instruments/ULN2803ADWRG4/296-35964-1-ND/4134939 | DigiKey | CHF 1.44 | 1 |  |  | CHF 1.44
4610X-2-105LF-ND | 4610X-102-105LF | Res Array 1M | https://www.bourns.com/docs/Product-Datasheets/4600x.pdf | https://www.digikey.ch/product-detail/de/bourns-inc/4610X-102-105LF/4610X-2-105LF-ND/1089224 | DigiKey | CHF 0.62 | 1 |  |  | CHF 0.62
4610X-2-102LF-ND | 4610X-102-102LF | Res Array 1k | https://www.bourns.com/docs/Product-Datasheets/4600x.pdf | https://www.digikey.ch/product-detail/de/bourns-inc/4610X-102-102LF/4610X-2-102LF-ND/1089222 | DigiKey | CHF 0.51 | 2 |  |  | CHF 1.02
455-2271-ND | B6B-XH-A(LF)(SN) | Balancer 6 | http://www.jst-mfg.com/product/pdf/eng/eXH.pdf | https://www.digikey.ch/products/de?keywords=B6B-XH-A(LF)(SN) | DigiKey | CHF 0.27 | 1 |  |  | CHF 0.27
455-2270-ND | B5B-XH-A(LF)(SN) | Balancer 5 | http://www.jst-mfg.com/product/pdf/eng/eXH.pdf | https://www.digikey.ch/product-detail/de/jst-sales-america-inc/B5B-XH-A-LF-SN/455-2270-ND/1530483 | DigiKey | CHF 0.27 | 1 |  |  | CHF 0.27
455-2252-ND | B7B-XH-A(LF)(SN) | Balancer 7 | http://www.jst-mfg.com/product/pdf/eng/eXH.pdf | https://www.digikey.ch/product-detail/de/jst-sales-america-inc/B7B-XH-A-LF-SN/455-2252-ND/1651050 | DigiKey | CHF 0.33 | 1 |  |  | CHF 0.33
160-1446-1-ND | LTST-C191KGKT | Grüne LED | http://optoelectronics.liteon.com/upload/download/DS22-2000-228/LTST-C191KGKT.PDF | https://www.digikey.ch/product-detail/de/lite-on-inc/LTST-C191KGKT/160-1446-1-ND/386834 | DigiKey | CHF 0.20 | 9 |  |  | CHF 1.77
445-1550-1-ND | MMZ1608S102ATA00 | FRB | https://product.tdk.com/info/en/catalog/datasheets/beads_commercial_signal_mmz1608_en.pdf | https://www.digikey.ch/product-detail/de/tdk-corporation/MMZ1608S102ATA00/445-1550-1-ND/571880 | DigiKey | CHF 0.10 | 1 |  |  | CHF 0.10
399-4925-1-ND | C0805C106K8PACTU | 10uF | https://content.kemet.com/datasheets/KEM_C1006_X5R_SMD.pdf | https://www.digikey.ch/product-detail/de/kemet/C0805C106K8PACTU/399-4925-1-ND/1090920 | DigiKey | CHF 0.16 | 3 |  |  | CHF 0.48
399-7932-1-ND | C0603C473K4RACTU | 470nF | https://content.kemet.com/datasheets/KEM_C1002_X7R_SMD.pdf | https://www.digikey.ch/product-detail/de/kemet/C0603C473K4RACTU/399-7932-1-ND/3471655 | DigiKey | CHF 0.12 | 4 |  |  | CHF 0.48
102-5890-1-ND | UJ2-MABH-4-SMT-TR | USB mini ab | https://www.cui.com/product/resource/uj2-mabh-smt.pdf | https://www.digikey.ch/product-detail/de/cui-inc/UJ2-MABH-4-SMT-TR/102-5890-1-ND/9838992 | Digikey | CHF 0.81 | 2 |  |  | CHF 1.62
768-1007-1-ND | FT232RL-REEL | Uart | https://www.ftdichip.com/Support/Documents/DataSheets/ICs/DS_FT232R.pdf | https://www.digikey.ch/product-detail/de/ftdi-future-technology-devices-international-ltd/FT232RL-REEL/768-1007-1-ND/1836402 | Digikey | CHF 4.41 | 1 |  |  | CHF 4.41
497-6063-ND | STM32F103C8T6 | Bootloader | https://www.st.com/resource/en/datasheet/stm32f103cb.pdf | https://www.digikey.ch/product-detail/de/stmicroelectronics/STM32F103C8T6/497-6063-ND/1646338 | DigiKey | CHF 5.69 | 1 |  |  | CHF 5.69
535-9754-1-ND | ASEM1-8.000MHZ-LC-T | 8 MHz | https://abracon.com/Oscillators/ASEM.pdf | https://www.digikey.ch/product-detail/de/abracon-llc/ASEM1-8.000MHZ-LC-T/535-9754-1-ND/1873288 | DigiKey | CHF 1.40 | 1 |  |  | CHF 1.40
36-3586KCT-ND | 3586KTR | Sicherungshalter | http://www.keyelco.com/product-pdf.cfm?p=314 | https://www.digikey.ch/product-detail/de/keystone-electronics/3586KTR/36-3586KCT-ND/7907919 | DigiKey | CHF 0.70 | 2 |  |  | CHF 1.40
F4201-ND | 0287020.PXCN | Sicherung 20A | https://www.littelfuse.com/~/media/automotive/datasheets/fuses/passenger-car-and-commercial-vehicle/blade-fuses/littelfuse_atof_datasheet.pdf | https://www.digikey.ch/product-detail/de/littelfuse-inc/0287020.PXCN/F4201-ND/2519821 | DigiKey | CHF 0.28 | 10 |  |  | CHF 2.80
620-1343-1-ND | A4988SETTR-T | MotorDriver | https://www.allegromicro.com/~/media/Files/Datasheets/A4988-Datasheet.ashx | https://www.digikey.ch/product-detail/de/allegro-microsystems/A4988SETTR-T/620-1343-1-ND/2238004 | DigiKey | CHF 3.08 | 1 |  |  | CHF 3.08
1528-1366-ND | 1528-1366-ND | Stepper | https://www.digikey.ch/product-detail/de/adafruit-industries-llc/858/1528-1366-ND/5629414 | https://www.digikey.ch/product-detail/de/adafruit-industries-llc/858/1528-1366-ND/5629414 | DigiKey | CHF 4.90 | 1 |  |  | CHF 4.90
277-1721-ND | TERM BLK 2POS SIDE ENT 3.5MM PCB | Term PCB | https://media.digikey.com/pdf/Data%20Sheets/Phoenix%20Contact%20PDFs/Combicon%20Compact%20Series.pdf | https://www.digikey.ch/product-detail/de/phoenix-contact/1984617/277-1721-ND/950849 | DigiKey | CHF 0.48 | 11 |  |  | CHF 5.28
493-2226-1-ND | UWT1H101MNL1GS | 100uF | https://products.nichicon.co.jp/en/pdf/XJA043/e-uwt.pdf | https://www.digikey.ch/product-detail/de/nichicon/UWT1H101MNL1GS/493-2226-1-ND/590201 | DigiKey | CHF 0.50 | 1 |  |  | CHF 0.50
399-1102-1-ND | C0603C224Z4VACTU | 220nF | https://content.kemet.com/datasheets/KEM_C1005_Y5V_SMD.pdf | https://www.digikey.ch/product-detail/de/kemet/C0603C224Z4VACTU/399-1102-1-ND/411377 | DigiKey | CHF 0.10 | 2 |  |  | CHF 0.20
603-1548-ND | AFB1212H-R00 | 82,7 CFM | https://www.delta-fan.com/Download/Spec/AFB1212H-R00.pdf | https://www.digikey.ch/product-detail/de/delta-electronics/AFB1212H-R00/603-1548-ND/2560671 | DigiKey | CHF 16.14 | 2 |  |  | CHF 32.28
277-1860-ND | TERM BLK 4POS SIDE ENT 3.5MM PCB | Term PCB | https://media.digikey.com/pdf/Data%20Sheets/Phoenix%20Contact%20PDFs/Combicon%20Compact%20Series.pdf | https://www.digikey.ch/product-detail/de/phoenix-contact/1984633/277-1860-ND/768668 | DigiKey | CHF 0.94 | 7 |  |  | CHF 6.58
S7013-ND | PPTC151LFBN-RC | buchse-arduino | https://media.digikey.com/pdf/Data%20Sheets/Sullins%20PDFs/Female_Headers.100_DS.pdf | https://www.digikey.ch/product-detail/de/sullins-connector-solutions/PPTC151LFBN-RC/S7013-ND/810153 | DigiKey | CHF 0.97 | 2 |  |  | CHF 1.94
160-1445-1-ND | LTST-C191KFKT | Orange LED | http://optoelectronics.liteon.com/upload/download/DS22-2000-222/LTST-C191KFKT.pdf | https://www.digikey.ch/product-detail/de/lite-on-inc/LTST-C191KFKT/160-1445-1-ND/386832 | DigiKey | CHF 0.26 | 2 |  |  | CHF 0.52
 |  |  |  |  |  |  |  | CHF 0.00 |  | CHF 115.01
 |  | Balancer Kabel |  | https://www.conrad.ch/de/p/modelcraft-lipo-balancer-verlaengerungskabel-ausfuehrung-ladegeraet-xh-ausfuehrung-akku-xh-geeignet-fuer-zellen-6-207156.html | Conrad | CHF 8.95 | 1 |  |  | CHF 8.95
 |  |  |  |  |  |  |  |  |  | CHF 0.00
 |  |  |  |  |  |  |  |  |  | CHF 0.00
 |  |  |  |  |  |  |  |  |  | CHF 8.95
 | DC Motor | 12V, 4krpm |  | https://www.banggood.com/de/Chihai-CHR-775S-Magnetic-Holzer-Encoder-DC-Motor-24_0V-8000RPM-12_0V-4000RPM-Robot-Driving-Motor-p-1390076.html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 | Banggood | CHF 15.71 | 4 |  | 8 | CHF 62.84 | CHF 125.68 | x
 | DCDC | 6-40V -> 1.2-36V |  | https://www.banggood.com/de/Geekcreit-DC-6-40V-To-1_2-36V-300W-20A-Constant-Current-Adjustable-Buck-Converter-Step-Down-Module-Board-p-1203369.html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 | Banggood | CHF 10.73 | 2 |  | 4 | CHF 21.46 | CHF 42.92 | x
 | Arduino Nano |  |  | https://www.banggood.com/de/ATmega328P-Nano-V3-Controller-Board-Compatible-Arduino-p-940937.html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 | Banggood | CHF 1.72 | 1 |  | 2 | CHF 1.72 | CHF 3.44 | x
 | Mecanum Wheels | 4pcs |  | https://www.banggood.com/de/Chihai-4pcs-60mm-Aluminium-Mecanum-Wheels-Universal-Wheels-with-8mm-Motor-Shaft-Coupling-for-Robot-Car-p-1501986.html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 | Banggood | CHF 40.61 | 1 |  | 2 | CHF 40.61 | CHF 81.22 | x
 | Motorhalterung | Metall? |  | https://www.banggood.com/de/Machifit-775-Motor-Bracket-Support-Motor-Fixed-Base-L-Shaped-Motor-Mounting-Bracket-p-1238099.html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 | Banggood | CHF 4.92 | 4 |  | 8 | CHF 19.68 | CHF 39.36 | x
 |  |  |  |  |  |  |  |  |  | CHF 146.31 | CHF 292.62
 |  |  |  |  |  |  |  |  |  | CHF 309.36
 |  | Batterie 10AH 6s |  | https://hobbyking.com/de_de/turnigy-high-capacity-10000mah-6s-12c-multi-rotor-lipo-pack-w-xt90.html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 | - | CHF 113.00 | -

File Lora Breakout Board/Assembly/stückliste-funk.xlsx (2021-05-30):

POS | Name | Wert | Datenblatt | Digikeylink | Lieferant | Preis | Anzahl |  | Bestellt
 | RN2483A-I/RM105 | LoRa | http://ww1.microchip.com/downloads/en/DeviceDoc/RN2483-Low-Power-Long-Range-LoRa-Technology-Transceiver-Module-Data-Sheet-DS50002346D.pdf | https://www.digikey.ch/products/de?keywords=RN2483A-I%2FRM105 | Digikey | CHF 12.92 | 5 | CHF 64.60 | 5 | CHF 64.60
 | LTST-C191KFKT | Orange LED | http://optoelectronics.liteon.com/upload/download/DS22-2000-222/LTST-C191KFKT.pdf | https://www.digikey.ch/product-detail/de/lite-on-inc/LTST-C191KFKT/160-1445-1-ND/386832 | Digikey | CHF 0.18 | 10 | CHF 1.84 | 15 | CHF 2.76
 | LTST-C191KGKT | Grüne LED | http://optoelectronics.liteon.com/upload/download/DS22-2000-228/LTST-C191KGKT.PDF | https://www.digikey.ch/product-detail/de/lite-on-inc/LTST-C191KGKT/160-1446-1-ND/386834 | Digikey | CHF 0.20 | 15 | CHF 2.96 | 20 | CHF 3.94
 | FT232RL-REEL | Uart | https://www.ftdichip.com/Support/Documents/DataSheets/ICs/DS_FT232R.pdf | https://www.digikey.ch/product-detail/de/ftdi-future-technology-devices-international-ltd/FT232RL-REEL/768-1007-1-ND/1836402 | Digikey | CHF 4.41 | 5 | CHF 22.05 | 5 | CHF 22.05
 | UJ2-MABH-4-SMT-TR | USB mini ab | https://www.cui.com/product/resource/uj2-mabh-smt.pdf | https://www.digikey.ch/product-detail/de/cui-inc/UJ2-MABH-4-SMT-TR/102-5890-1-ND/9838992 | Digikey | CHF 0.81 | 5 | CHF 4.05 | 5 | CHF 4.05
 | CL21A106KPFNNNG | 10uF | http://www.samsungsem.com/kr/support/product-search/mlcc/__icsFiles/afieldfile/2019/05/10/19-CL21A106KPFNNNG.pdf | https://www.digikey.ch/product-detail/de/samsung-electro-mechanics/CL21A106KPFNNNG/1276-6456-1-ND/5958084 | Digikey | CHF 0.13 | 5 | CHF 0.65 | 7 | CHF 0.91
 | AP2120N-3.3TRG1 | 3.3V | https://www.diodes.com/assets/Datasheets/AP2120.pdf | https://www.digikey.ch/product-detail/de/diodes-incorporated/AP2120N-3.3TRG1/AP2120N-3.3TRG1DICT-ND/4505261 | Digikey | CHF 0.36 | 5 | CHF 1.80 | 7 | CHF 2.52
 | CL21B105KAFNNNE | 1uF | http://www.samsungsem.com/kr/support/product-search/mlcc/__icsFiles/afieldfile/2019/06/18/CL21B105KAFNNNE-19.pdf | https://www.digikey.ch/product-detail/de/samsung-electro-mechanics/CL21B105KAFNNNE/1276-1066-1-ND/3889152 | Digikey | CHF 0.08 | 10 | CHF 0.77 | 15 | CHF 1.16
 | RECE.20279.001E.01 | U.FL (IPEX) | https://cdn.taoglas.com/datasheets/RECE.20279.001E.01.pdf | https://www.digikey.ch/product-detail/de/taoglas-limited/RECE.20279.001E.01/931-1107-1-ND/2332746 | Digikey | CHF 0.72 | 10 | CHF 7.20 | 15 | CHF 10.80
 |  |  |  | -
 |  |  |  | -
 |  |  |  | -
 |  |  |  | -
 |  |  |  | - |  |  |  | CHF 105.91 |  | CHF 112.78
 |  |  |  | -
 |  |  |  | -
 |  |  |  | -
 |  |  |  | -
 |  |  |  | -
 |  |  |  | -
 |  |  |  | -
 |  |  |  | -
 |  |  |  | -
 |  |  |  | -
 |  |  |  | -
 |  |  |  | -
 |  |  |  | -

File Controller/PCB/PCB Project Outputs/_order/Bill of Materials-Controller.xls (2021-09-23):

Comment | Description | Designator | Footprint | LibRef | Manufacturer | Manufacturer Part Number | Note | Quantity | Supplier | Supplier Part Number | Library Reference
1uF | capacitor | C1, C3 | CAP_0603i_1608m -N | Cap |  |  |  | 2 |  |  | Cap
100nF | capacitor | C2, C4, C6, C7, C8, C9, C11, C12, C13, C14, C15, C17, C18, C19, C20, C21 | CAP_0402i_1005m -N | Cap |  |  |  | 16 |  |  | Cap
10 uF | capacitor | C5, C16 | CAP_0603i_1608m -N | Cap |  |  |  | 2 |  |  | Cap
Grün | LED; SMD; 0603; grün; 35mcd; 1.6x0.8x0.55mm; 130Â°; 2Ã·2.V; 20mA | D1, D3, D5, D7, D8 | *0603 | LTST-C191KGKT |  |  |  | 5 |  |  | LTST-C191KGKT
Orange | LED; SMD; 0603; orange; 45-90mcd; 1.6x0.8x0.55mm; 130Â°; 2Ã·2.4V; 20mA , LED; SMD; 0603; grün; 35mcd; 1.6x0.8x0.55mm; 130Â°; 2Ã·2.V; 20mA | D2, D4, D6 | *0603 | LTST-C191KFKT, LTST-C191KGKT |  |  |  | 3 |  |  | LTST-C191KFKT, LTST-C191KGKT
FT232RL-TUBE | USB-to-UART 1-CH 256byte FIFO 5V 28-Pin SSOP Tube | IC1 | *SSOP28-LD | FT232RL-TUBE |  |  |  | 1 |  |  | FT232RL-TUBE
UJ2-MABH-4-SMT | Mini AB, USB 2.0, 1 A, Right Angle, Surface Mount _SMT_, USB Receptacle | J1 | *CUI_UJ2-MABH-4-SMT_UJ2-MABH-4-SMT(Primary) | UJ2-MABH-4-SMT |  |  |  | 1 |  |  | UJ2-MABH-4-SMT
Joystick |  | J2, J3 | Joystick | Joystick |  |  |  | 2 |  |  | Joystick
Inductor | Inductor | L1 | IND_0805I_2013-L | Inductor |  |  |  | 1 |  |  | Inductor
Header 7H | Header, 7-Pin, Right Angle | P1 | HDR1X7H | Header 7H |  |  |  | 1 |  |  | Header 7H
Batterie | Single Pad or Testpoint | P2 | MotConnector | Pad, double |  |  |  | 1 |  |  | Pad, double
ON-OFF | Single Pad or Testpoint | P3 | MotConnector | Pad, double |  |  |  | 1 |  |  | Pad, double
Header 5H | Header, 5-Pin, Right Angle | P4 | HDR1X5H | Header 5H |  |  |  | 1 |  |  | Header 5H
Tag-Connect TC2050-IDC-NL-No pin assigned | 10-pin pogo pin programing port | P5 | TAG-CONNECT TC2050-IDC-NL 10-Pin | Tag-Connect TC2050-IDC-NL-No pin assigned |  |  |  | 1 |  |  | Tag-Connect TC2050-IDC-NL-No pin assigned
Header 2 | Header, 2-Pin | P6 | HDR1X2 | Header 2 |  |  |  | 1 |  |  | Header 2
Hirose U.FL-R-SMT-1(10) | U.FL | P7 | Hirsoe U.FL-R-SMT-1(10) | Hirose U.FL-R-SMT-1(10) |  |  |  | 1 |  |  | Hirose U.FL-R-SMT-1(10)
AO4407A | Mosfet p-Ch -30v -12a 8-Soic - Ao4407a | Q1 | SOIC127P600X175-8N | AO4407A |  |  |  | 1 |  |  | AO4407A
1k | Resistor | R1, R2, R3, R4 | RES_0402i_1005m -N | Res |  |  |  | 4 |  |  | Res
10K | Resistor | R5, R6, R9, R10, R11, R12 | RES_0402i_1005m -N | Res |  |  |  | 6 |  |  | Res
330 | Resistor | R7, R8 | RES_0402i_1005m -N | Res |  |  |  | 2 |  |  | Res
270 | Resistor | R13, R14, R15 | RES_0402i_1005m -N | Res |  |  |  | 3 |  |  | Res
20K | Resistor | R16, R17 | RES_0402i_1005m -N | Res |  |  |  | 2 |  |  | Res
100K | Resistor | R18 | RES_0402i_1005m -N | Res |  |  |  | 1 |  |  | Res
Part Number: MMBT3904-7-F | Transistor SMD | T1, T2, T3, T4, T5 | SOT-23-M | MMBT3904-7-F |  |  |  | 5 |  |  | MMBT3904-7-F
AZ1117EH-3.3TRG1 | Linear Voltage Regulator IC 1 Output 1A SOT-223 | U1, U2 | SOT230P700X180-4N | AZ1117EH-3.3TRG1 |  |  |  | 2 |  |  | AZ1117EH-3.3TRG1
BUTTON |  | U3, U5 | RND 210-00206 | BUTTON |  |  |  | 2 |  |  | BUTTON
BMG250 | BMG250 Series 3.6 V 3200 Hz 850 ÂµA Low Noise Low Power Triaxial Gyroscope-LGA-14 | U4 | XDCR_BMG250 | BMG250 |  |  |  | 1 |  |  | BMG250
STM32F730R8T6 | IC MCU 32BIT 64KB FLASH 64LQFP | U6 | FP-LQFP64-5W-MFG | CMP-12105-000011-1 | STMicroelectronics | STM32F730R8T6 |  | 1 |  |  | CMP-12105-000011-1
RN2483-I/RM095 | Sub-GHz Dual Band Long Range Transceiver LoRa Module | U7 | *MICROCHIP_RN2483-I/RM095 | RN2483-I/RM095 |  |  |  | 1 |  |  | RN2483-I/RM095
LoRa Modul |  | U8 | LoRA - w/o holes | LoRa Modul |  |  |  | 1 |  |  | LoRa Modul

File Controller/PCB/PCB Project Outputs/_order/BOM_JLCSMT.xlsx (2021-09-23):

Comment | Designator | Footprint | LCSC Part #（optional）
CL10A106KP8NNNC | C5,C16 | 0603 | C19702 (https://lcsc.com/product-detail/Multilayer-Ceramic-Capacitors-MLCC-SMD-SMT_SAMSUNG_CL10A106KP8NNNC_10uF-106-10-10V_C19702.html/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)
CL10A105KB8NNNC | C1,C3 | 0603 | C15849 (https://lcsc.com/product-detail/Multilayer-Ceramic-Capacitors-MLCC-SMD-SMT_SAMSUNG_CL10A105KB8NNNC_1uF-105-10-50V_C15849.html/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)
CL05B104KO5NNNC | C2,C4,C6,C7,C17,C18,C20,C21,C8,C9,C11,C12,C13,C14,C15,C19 | 0402 | C1525 (https://lcsc.com/product-detail/Multilayer-Ceramic-Capacitors-MLCC-SMD-SMT_SAMSUNG_CL05B104KO5NNNC_100nF-104-10-16V_C1525.html/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)
19-217/GHC-YR1S2/3T | D1,D3,D5,D7,D8 | 0603 | C72043 (https://lcsc.com/product-detail/Light-Emitting-Diodes-LED_0603-Green-light_C72043.html/?href=jlc-SMT)
KT-0603R | D2,D4,D6 | LED_0603 | C2286 (https://lcsc.com/product-detail/Light-Emitting-Diodes-LED_Hubei-KENTO-Elec-KT-0603R_C2286.html/?href=jlc-SMT)
FT232RL-REEL | IC1 | SSOP-28_5.3x10.2x0.65P | C8690 (https://lcsc.com/product-detail/USB_FTDI_FT232RL-REEL_FT232RL-REEL_C8690.html/?href=jlc-SMT)
GZ2012D601TF | L1 | 0805 | C1017 (https://lcsc.com/product-detail/Beads_Sunlord-GZ2012D601TF_C1017.html/?href=jlc-SMT)
AO4407C | Q1 | SOP-8_3.9x4.9x1.27P | C469397 (https://lcsc.com/product-detail/MOSFET_Alpha-Omega-Semicon-AO4407C_C469397.html/?href=jlc-SMT)
0402WGF1001TCE | R1,R2,R3,R4 | 0402 | C11702 (https://lcsc.com/product-detail/Chip-Resistor-Surface-Mount_Uniroyal-Elec-0402WGF1001TCE_C11702.html/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)
0402WGF1002TCE | R5,R6,R9,R10,R11,R12 | 0402 | C25744 (https://lcsc.com/product-detail/Chip-Resistor-Surface-Mount_Uniroyal-Elec-0402WGF1002TCE_C25744.html/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)
0402WGF3301TCE | R7,R8 | 0402 | C25890 (https://lcsc.com/product-detail/Chip-Resistor-Surface-Mount_Uniroyal-Elec-0402WGF3301TCE_C25890.html/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)
0603WAF2700T5E | R13,R14,R15 | 0603 | C22966 (https://lcsc.com/product-detail/Chip-Resistor-Surface-Mount_Uniroyal-Elec-0603WAF2700T5E_C22966.html/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)
0402WGF2002TCE | R16,R17 | 0402 | C25765 (https://lcsc.com/product-detail/Chip-Resistor-Surface-Mount_Uniroyal-Elec-0402WGF2002TCE_C25765.html/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)
0402WGF1003TCE | R18 | 0402 | C25741 (https://lcsc.com/product-detail/Chip-Resistor-Surface-Mount_Uniroyal-Elec-0402WGF1003TCE_C25741.html/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)
MMBT3904-7-F | T1,T2,T3,T4,T5 | SOT-23-3 | C94514 (https://lcsc.com/product-detail/Transistors-NPN-PNP_DIODES_MMBT3904-7-F_MMBT3904-7-F_C94514.html/?href=jlc-SMT)
AZ1117EH-3.3TRG1 | U1,U2 | SOT-223 | C108494 (https://lcsc.com/product-detail/Low-Dropout-Regulators-LDO_DIODES_AZ1117EH-3-3TRG1_AZ1117EH-3-3TRG1_C108494.html/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)
STM32F405RGT6 | U6 | LQFP-64_10.0x10.0x0.5P | C15742 (https://lcsc.com/product-detail/ST-Microelectronics_STMicroelectronics_STM32F405RGT6_STM32F405RGT6_C15742.html/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)

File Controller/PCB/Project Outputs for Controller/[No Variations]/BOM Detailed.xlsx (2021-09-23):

Designator | Description | Comment | Footprint | Quantity
 |  | LoRa Modul | LoRA | 1
C1 | capacitor | 22 pF | CAP_0603i_1608m -N | 1
C2 | capacitor | 22 pF | CAP_0603i_1608m -N | 1
C3 | capacitor | 100nF | CAP_0603i_1608m -N | 1
C4 | capacitor | 100nF | CAP_0603i_1608m -N | 1
C5 | 10 uF 10 V | Capacitor_0805 | 10uF_0805_Chip2PinSM127P600-8N | 1
C6 | capacitor | 1 uF 10V | CAP_0805i_2012m -N | 1
C7 |  | Capacitor_0603 | C_0603_Chip2PinSM127P600-8N | 1
C8 | capacitor | 1 uF 10V | CAP_0805i_2012m -N | 1
C9 | 10 uF 25V | Capacitor_0603 | C_0603_Chip2PinSM127P600-8N | 1
C10 |  | Capacitor_0603 | C_0603_Chip2PinSM127P600-8N | 1
C11 | 10 uF 25V | Capacitor_0603 | C_0603_Chip2PinSM127P600-8N | 1
C12 | 10 uF 25 V | Capacitor_0603 | C_0603_Chip2PinSM127P600-8N | 1
C13 |  | Capacitor_0603 | C_0603_Chip2PinSM127P600-8N | 1
C14 | capacitor | 100nF | CAP_0603i_1608m -L | 1
C15 | capacitor | 10 uF 10 V | CAP_0805i_2012m -N | 1
C16 | capacitor | 100nF | CAP_0603i_1608m -L | 1
C17 | capacitor | 22 pF | CAP_0603i_1608m -N | 1
C18 | capacitor | 0.1 uF | CAP_0603i_1608m -N | 1
C19 | capacitor | 0.1 uF | CAP_0603i_1608m -N | 1
C20 | capacitor | 22 pF | CAP_0603i_1608m -N | 1
C21 | capacitor | 0.1 uF | CAP_0603i_1608m -N | 1
C22 | capacitor | 0.1 uF | CAP_0603i_1608m -N | 1
C23 | capacitor | 0.1 uF | CAP_0603i_1608m -N | 1
C24 | capacitor | 0.1 uF | CAP_0603i_1608m -N | 1
C25 | capacitor | 0.1 uF | CAP_0603i_1608m -N | 1
C26 | capacitor | 0.1 uF | CAP_0603i_1608m -N | 1
C27 | capacitor | 10 uF 10 V | CAP_0805i_2012m -N | 1
CR1 |  | STM32F103C8T6 | LQFP-48 | 1
D1 | LED; SMD; 0603; grün; 35mcd; 1.6x0.8x0.55mm; 130Â°; 2Ã·2.V; 20mA | Grün | *0603 | 1
D2 | LED; SMD; 0603; orange; 45-90mcd; 1.6x0.8x0.55mm; 130Â°; 2Ã·2.4V; 20mA | Orange | *0603 | 1
D3 | LED; SMD; 0603; grün; 35mcd; 1.6x0.8x0.55mm; 130Â°; 2Ã·2.V; 20mA | Grün | *0603 | 1
D4 |  | BAT54T1G | BAT54T1G_SODFL371X135-2N | 1
D5 | LED; SMD; 0603; grün; 35mcd; 1.6x0.8x0.55mm; 130Â°; 2Ã·2.V; 20mA | Grün | *0603 | 1
D6 | LED; SMD; 0603; orange; 45-90mcd; 1.6x0.8x0.55mm; 130Â°; 2Ã·2.4V; 20mA | Orange | *0603 | 1
D7 |  | 1N4148 | 1N4148_SODFL127P600-8N | 1
D8 |  | 1N4148 | 1N4148_SODFL127P600-8N | 1
D9 | LED; SMD; 0603; grün; 35mcd; 1.6x0.8x0.55mm; 130Â°; 2Ã·2.V; 20mA | Grün | *0603 | 1
F1 |  | Fuse | FUSE-3586KTR | 1
IC1 | USB-to-UART 1-CH 256byte FIFO 5V 28-Pin SSOP Tube | FT232RL-TUBE | *SSOP28-LD | 1
J1 | Mini AB, USB 2.0, 1 A, Right Angle, Surface Mount _SMT_, USB Receptacle | UJ2-MABH-4-SMT | *CUI_UJ2-MABH-4-SMT_UJ2-MABH-4-SMT(Primary) | 1
J2 | Mini AB, USB 2.0, 1 A, Right Angle, Surface Mount _SMT_, USB Receptacle | UJ2-MABH-4-SMT | *CUI_UJ2-MABH-4-SMT_UJ2-MABH-4-SMT(Primary) | 1
J3 |  | Joystick | Joystick | 1
J4 |  | Joystick | Joystick | 1
L1 |  | Inductor_0805 | 0805_INDC2012X12N | 1
L2 | Inductor | Inductor | Murata Inductor 2900 sch | 1
P1 | Header, 4-Pin | Header 4 | HDR1X4 | 1
P2 | Header, 5-Pin | SWIM | HDR1X5 | 1
P3 | Header, 5-Pin | SWD | HDR1X5 | 1
P6 | Single Pad or Testpoint | ON-OFF | MotConnector | 1
P7 | Connector; IDC, Male Header, Thru-Hole; 20 Position; Vertical; Pitch 2.54 mm; B | IDC-20 | IDC-20 | 1
P8 | Single Pad or Testpoint | Batterie | MotConnector | 1
R1 | Resistor | 1000 | RES_0603i_1608m -N | 1
R2 | Resistor | 1000 | RES_0603i_1608m -N | 1
R3 | Resistor | 100K | RES_0603i_1608m -N | 1
R4 | Resistor | 100K | RES_0603i_1608m -N | 1
R5 | Resistor | 390 | RES_0603i_1608m -N | 1
R6 | Resistor | 10K | RES_0603i_1608m -N | 1
R7 | Resistor | 10K | RES_0603i_1608m -N | 1
R8 | Resistor | 10K | RES_0603i_1608m -N | 1
R9 | Resistor | 220 | RES_0603i_1608m -N | 1
R10 | Resistor | 220 | RES_0603i_1608m -N | 1
R11 | Resistor | 220 | RES_0603i_1608m -N | 1
R12 | Resistor | 100 | RES_0603i_1608m -N | 1
R13 | Resistor | 22 | RES_0603i_1608m -N | 1
R14 | Resistor | 22 | RES_0603i_1608m -N | 1
R15 | Resistor | 22 | RES_0603i_1608m -N | 1
R16 | Resistor | 22 | RES_0603i_1608m -N | 1
R17 | Resistor | 22 | RES_0603i_1608m -N | 1
R18 | Resistor | 1K | RES_0603i_1608m -N | 1
R19 |  | Resistor_0603 | R_0603_Chip2PinSM127P600-8N | 1
R20 |  | Resistor_0603 | R_0603_Chip2PinSM127P600-8N | 1
R21 | Resistor | 1000 | RES_0603i_1608m -N | 1
R22 | Resistor | 1000 | RES_0603i_1608m -N | 1
R23 | Resistor | 1K | RES_0603i_1608m -N | 1
R24 | Resistor | 1K | RES_0603i_1608m -N | 1
R25 | 560 K | Resistor_0603 | R_0603_Chip2PinSM127P600-8N | 1
R26 | 50 | Resistor_0603 | R_0603_Chip2PinSM127P600-8N | 1
R27 | Resistor | 10 K | RES_0603i_1608m -N | 1
R28 | Resistor | 390 | RES_0603i_1608m -N | 1
R29 | Resistor | 10K | RES_0603i_1608m -N | 1
R30 | Resistor | 10K | RES_0603i_1608m -N | 1
R31 | Resistor | 10K | RES_0603i_1608m -N | 1
R32 | Resistor | 10K | RES_0603i_1608m -N | 1
R33 | Resistor | 10K | RES_0603i_1608m -N | 1
R34 | Resistor | 10K | RES_0603i_1608m -N | 1
R35 | Resistor | 10K | RES_0603i_1608m -N | 1
R36 | Resistor | 10K | RES_0603i_1608m -N | 1
R37 | Resistor | 10K | RES_0603i_1608m -N | 1
S1 | Switch | SW PB | B3SL-1002P | 1
U1 |  | OLED_Driver | FAN5331S_SOT23127P600-8N | 1
U2 | 3.3V Voltage Regulator | Part Number: AP2120N-3.3TRG1 | SOT-23-M | 1
U3 | STM32 Series 32-bit 256 kB Flash 64 kB RAM ARM Based Microcontroller -LQFP-100 | STM32F107VCT6 | *QFP50P1600X1600X160-100N | 1
U4 | Ldo.Vreg Pos 3, 3v 1a Sot223 | AZ1117EH-3.3TRG1 | *SOT230P700X180-4N | 1
X1 |  | Molex_FlatFlex-to-Board | MOLEX_FTB_30 | 1
 | Industrial Ceramic Resonator | XTAL3 | TSX-3225 2*2.5 | 1
Y2 | Industrial Ceramic Resonator | XTAL3 | TSX-3225 2*2.5 | 1

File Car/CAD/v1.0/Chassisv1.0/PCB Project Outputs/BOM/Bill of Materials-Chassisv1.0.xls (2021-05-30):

Comment | Description | Designator | Footprint | LibRef | Manufacturer | Manufacturer Part Number | Note | Quantity | Supplier | Supplier Part Number | Library Reference
Fuse |  | *1 | FUSE-3586KTR | Fuse |  |  |  | 1 |  |  | Fuse
DRV8840PWP | DC Motor Driver | B1, B2, B3, B4 | 28-Pin HTSSOP | DRV8840PWP |  |  |  | 4 |  |  | DRV8840PWP
10uF | capacitor | C1, C34, C43 | CAP_0805i_2012m -L | Cap |  |  |  | 3 |  |  | Cap
1uF | capacitor | C2 | CAP_0805i_2012m -L | Cap |  |  |  | 1 |  |  | Cap
100uF | polarised capacitor alternative | C10 | Cap_F-Type-Package | Cap pol2 |  |  |  | 1 |  |  | Cap pol2
220n | capacitor | C12, C13 | CAP_0603i_1608m -N | Cap |  |  |  | 2 |  |  | Cap
10nF | capacitor | C14, C15, C22, C23 | CAP_0603i_1608m -N | Cap |  |  |  | 4 |  |  | Cap
100nF | capacitor | C9, C11, C16, C17, C18, C19, C24, C25, C26, C27, C30, C31, C35, C36, C37, C38, C39, C40, C41, C42, C46, C47, C48, C49, C50 | CAP_0603i_1608m -N | Cap |  |  |  | 20 |  |  | Cap
470nF | capacitor | C20, C21, C28, C29 | CAP_0603i_1608m -N | Cap |  |  |  | 4 |  |  | Cap
22pF | capacitor | C32, C33, C44, C45 | CAP_0603i_1608m -N | Cap |  |  |  | 4 |  |  | Cap
100pF | capacitor | C51 | CAP_0603i_1608m -N | Cap |  |  |  | 1 |  |  | Cap
STM32F103C8T6 | uC | CR1 | LQFP-48 | STM32F103C8T6 |  |  |  | 1 |  |  | STM32F103C8T6
Grün | LED | D1, D2, D3, D10, D11, D12, D13, D14, D16 | *0603 | LTST-C191KGKT |  |  |  | 9 |  |  | LTST-C191KGKT
Orange | LED | D15, D17 | *0603 | LTST-C191KFKT |  |  |  | 2 |  |  | LTST-C191KFKT
FT232RL-TUBE | USB-to-UART 1-CH | IC1 | *SSOP28-LD | FT232RL-TUBE |  |  |  | 1 |  |  | FT232RL-TUBE
Balancer | XH connector, 6 way | J1 | SHDR6W64P0X250_1X6_1740X575X700P | B6B-XH-A(LF)(SN) |  |  |  | 1 |  |  | B6B-XH-A(LF)(SN)
Balancer | XH connector, 5 way | J2 | SHDR5W64P0X250_1X5_1490X575X700P | B5B-XH-A(LF)(SN) |  |  |  | 1 |  |  | B5B-XH-A(LF)(SN)
Balancer | XH connector, 7 way | J3 | SHDR7W64P0X250_1X7_1990X575X700P | B7B-XH-A(LF)(SN) |  |  |  | 1 |  |  | B7B-XH-A(LF)(SN)
Front-LEFT | 4 Term 3.5 mm | J4, J5, J6, J7 J8, J9, J10, J13 | *PHOENIX_1751264 | Terminal 4 Pin |  |  |  | 3 |  |  | Terminal 4 Pin
USB Mini | Mini AB, USB 2.0 | J11, J12 | *CUI_UJ2-MABH-4-SMT_UJ2-MABH-4-SMT(Primary) | UJ2-MABH-4-SMT |  |  |  | 1 |  |  | UJ2-MABH-4-SMT
Inductor | Inductor | L1 | IND_0603i_1608m -L | Inductor |  |  |  | 1 |  |  | Inductor
Battery + | Single Pad | P1 | PIN1 | Pad |  |  |  | 1 |  |  | Pad
Header 2 | 2 Term 3.5 mm | P2, P3, P5, P6, P9, P10, P11, P12, P13, P14, P21 | 3.5MM Phoenix Contact 1984617 | Header 2 |  |  |  | 11 |  |  | Header 2
Battery - | Single Pad | P4 | PIN1 | Pad |  |  |  | 1 |  |  | Pad
NP | Header, 8-Pin | P7 | HDR1X8 | Header 8 |  |  |  | 1 |  |  | Header 8
Header 7 | Header, 7-Pin | P8 | HDR1X7 | Header 7 |  |  |  | 1 |  |  | Header 7
Pad | Single Pad or Testpoint | P15, P16, P17, P18, P19, P20, P22, P23, P24, P25, P26, P27, P28, P29, P31, P32, P33, P34, P35, P36, P37, P38, P39, P40 | PIN1 | Pad |  |  |  | 24 |  |  | Pad
IDC-20 | Connector 20 2.54 mm; B | P30 | IDC-20 | IDC-20 |  |  |  | 1 |  |  | IDC-20
SWIM | Header, 5-Pin | P41 | HDR1X5 | Header 5 |  |  |  | 1 |  |  | Header 5
SWD | Header, 5-Pin | P42 | HDR1X5 | Header 5 |  |  |  | 1 |  |  | Header 5
Program | Header, 4-Pin | P43 | HDR1X4 | Header 4 |  |  |  | 1 |  |  | Header 4
PMOS | P-Channel MOSFET, 35 A, 20 V, 8-Pin PowerPAK 1212 Vishay | Q1 | SIS862DNT1GE3 | SI7615ADN-T1-GE3 |  |  |  | 1 |  |  | SI7615ADN-T1-GE3
10k | Resistor | R1, R3, R4, R5, R49, R50, R60, R62, R69 | RES_0805i_2012m -N | Res |  |  |  | 9 |  |  | Res
100k | Resistor | R2, R11, R12, R47, R48, R59, R61 | RES_0805i_2012m -N | Res |  |  |  | 7 |  |  | Res
9.1k | Resistor | R6 | RES_0805i_2012m -N | Res |  |  |  | 1 |  |  | Res
11k | Resistor | R7 | RES_0805i_2012m -N | Res |  |  |  | 1 |  |  | Res
15k | Resistor | R8 | RES_0805i_2012m -N | Res |  |  |  | 1 |  |  | Res
20k | Resistor | R9 | RES_0805i_2012m -N | Res |  |  |  | 1 |  |  | Res
33k | Resistor | R10 | RES_0805i_2012m -N | Res |  |  |  | 1 |  |  | Res
NP | Resistor, [NoValue] | R16, R20, R21, R22, R23, R24, R25, R26, R27, R30, R31, R34, R35, R36, R37, R38, R39, R40 | RES_0603i_1608m -N | Res |  |  |  | 18 |  |  | Res
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

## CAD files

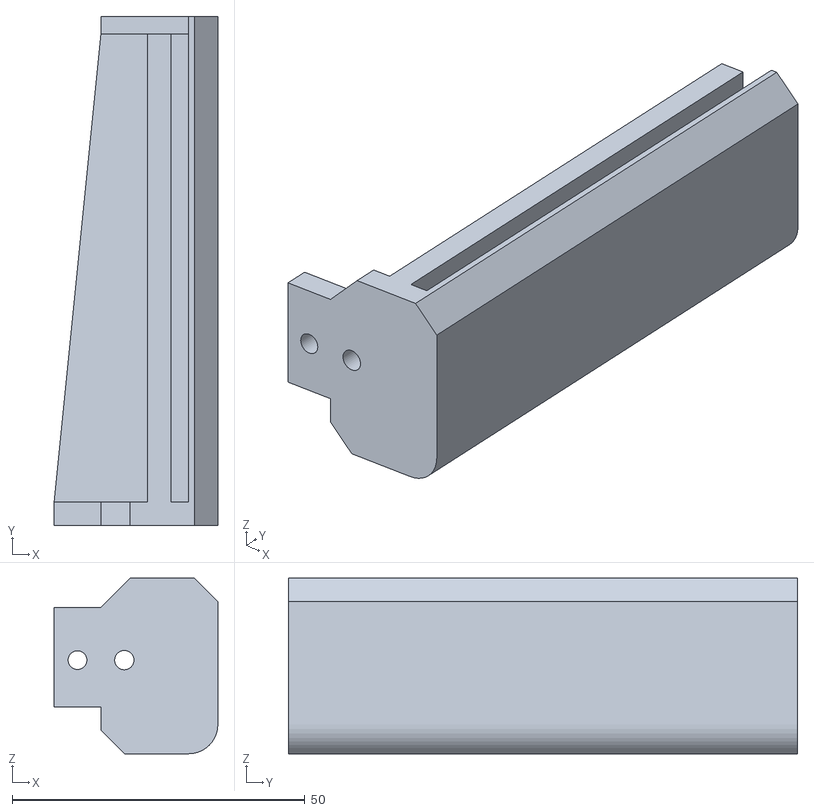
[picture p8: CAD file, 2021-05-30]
Car/3d modell/3dprint/base-ecke-halter-rechts.STL
28.0 x 87.0 x 30.0

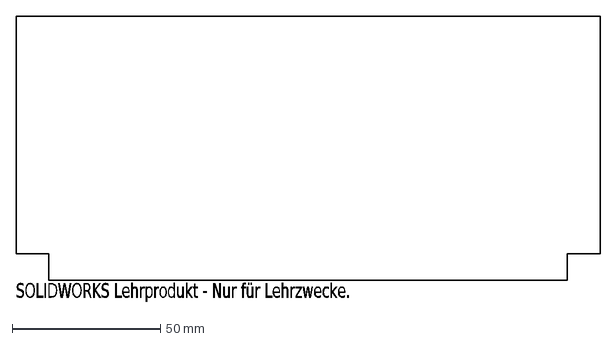
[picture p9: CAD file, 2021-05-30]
Car/3d modell/Plexiglas/dfx/wall_B.DXF
SOLIDWORKS Lehrprodukt - Nur für Lehrzwecke.

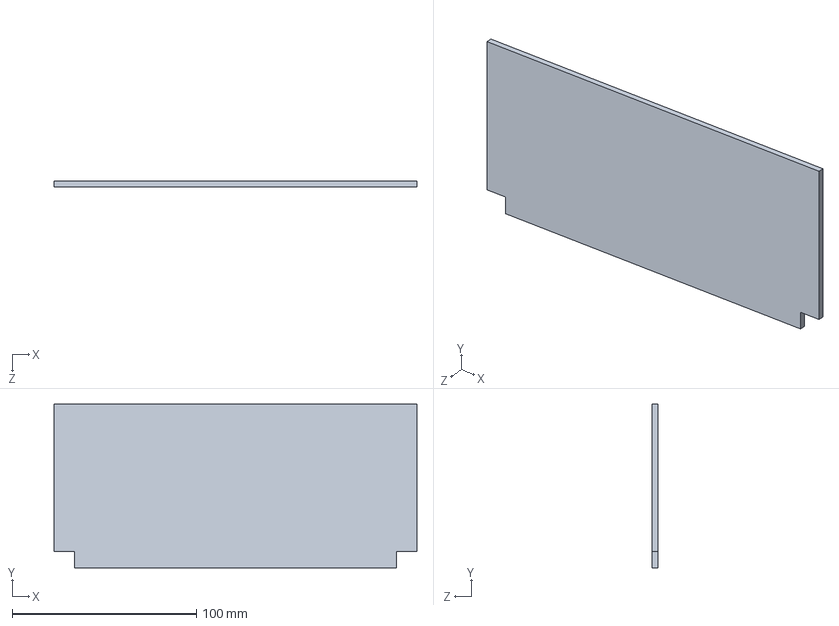
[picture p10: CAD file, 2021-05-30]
Car/3d modell/Plexiglas/wall_B.SLDPRT
197.0 x 89.0 x 3.00 mm

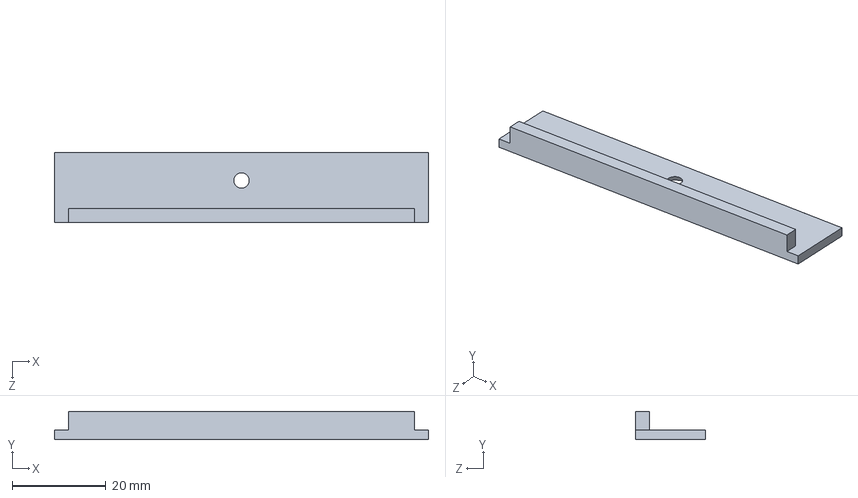
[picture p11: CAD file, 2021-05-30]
Car/3d modell/Solidworks Files/Scheinwerfer_deckel.SLDPRT
80.0 x 6.00 x 15.0 mm

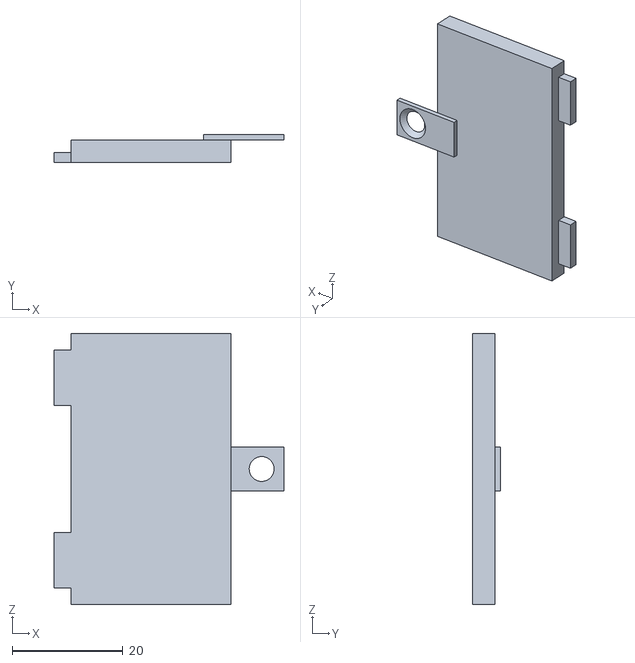
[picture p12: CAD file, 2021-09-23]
Controller/Assembly/batterie_deckel.STL
41.5 x 5.00 x 49.0

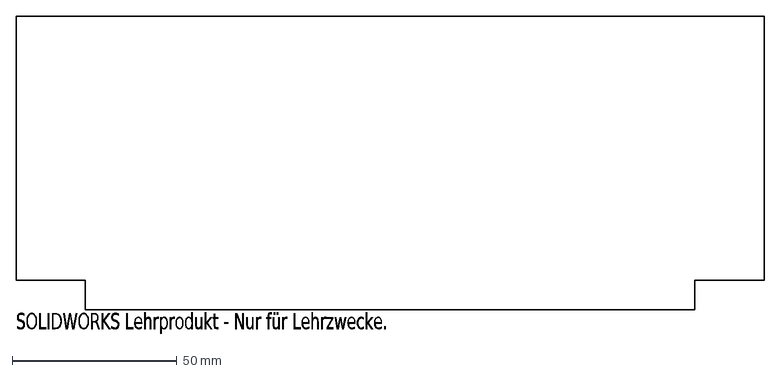
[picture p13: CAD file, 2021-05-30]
Car/3d modell/Plexiglas/dfx/wall_L_R.DXF
SOLIDWORKS Lehrprodukt - Nur für Lehrzwecke.

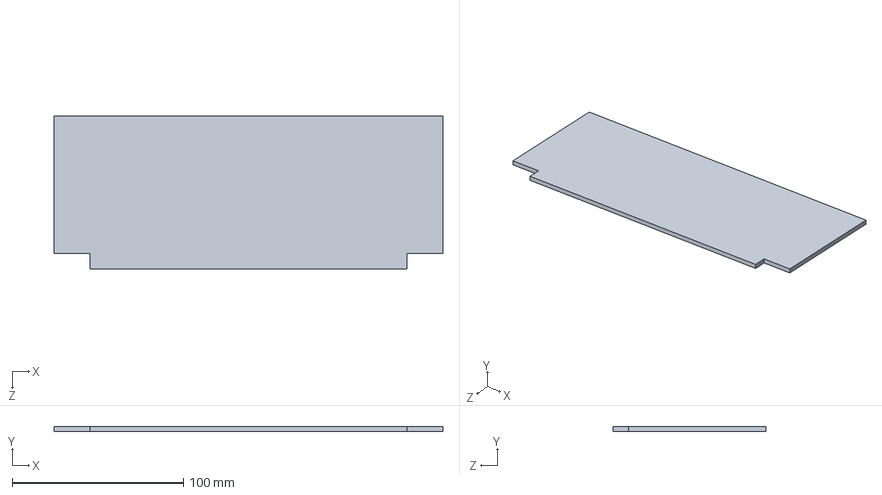
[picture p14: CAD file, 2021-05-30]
Car/3d modell/Plexiglas/wall_L_R.SLDPRT
227.0 x 3.00 x 89.0 mm

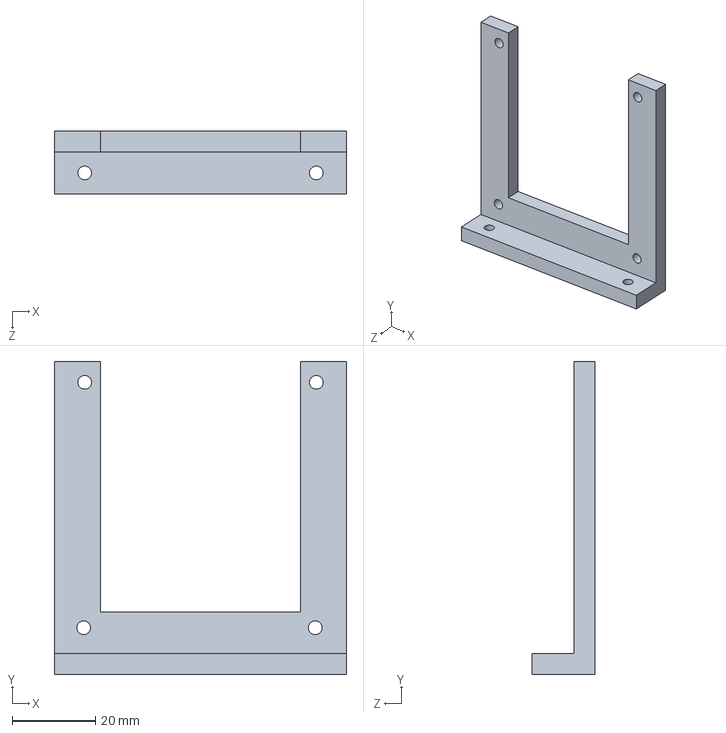
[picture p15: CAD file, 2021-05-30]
Car/3d modell/Solidworks Files/LORA_mount.SLDPRT
70.0 x 75.0 x 15.0 mm

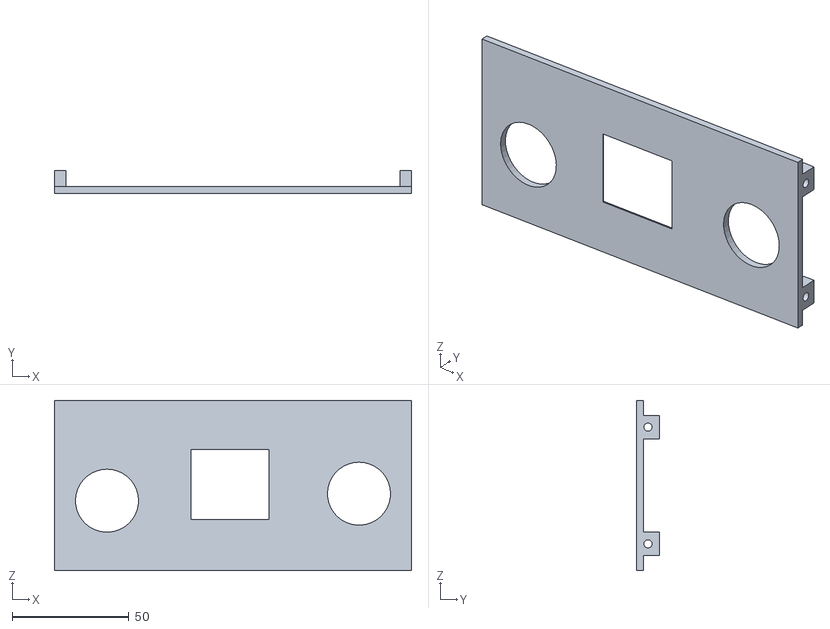
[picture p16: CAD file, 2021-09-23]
Controller/Assembly/gehaeuse_top.STL
153.0 x 10.0 x 73.0

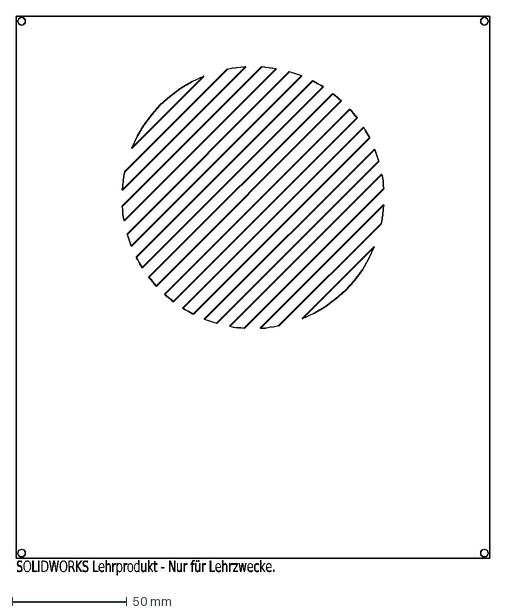
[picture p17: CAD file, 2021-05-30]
Car/3d modell/Plexiglas/dfx/roof1.DXF
SOLIDWORKS Lehrprodukt - Nur für Lehrzwecke.

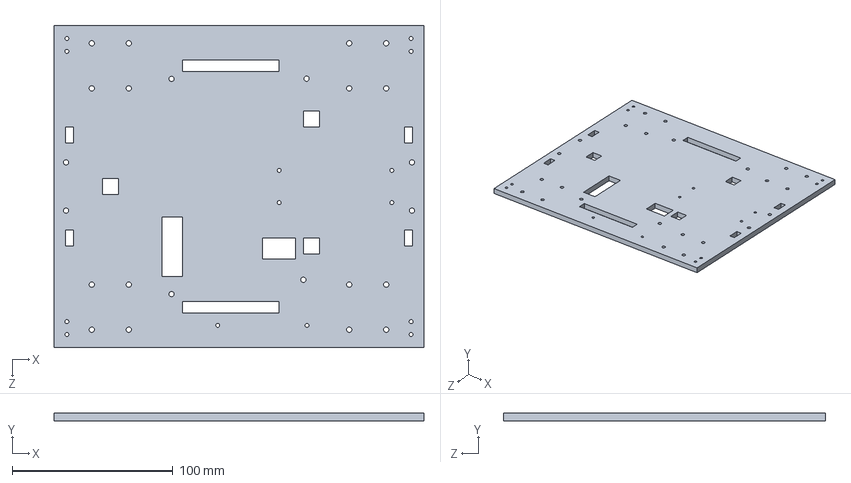
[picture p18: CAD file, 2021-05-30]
Car/3d modell/Solidworks Files/base_plate.SLDPRT
230.0 x 5.00 x 200.0 mm

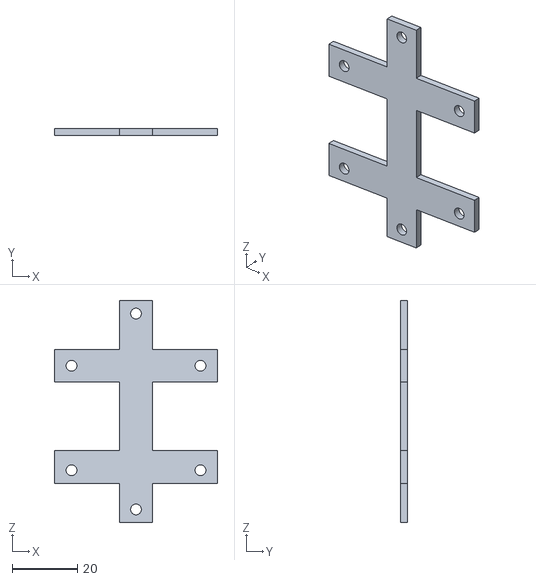
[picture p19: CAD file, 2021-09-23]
Controller/Assembly/oled_halter.STL
50.0 x 2.00 x 68.0

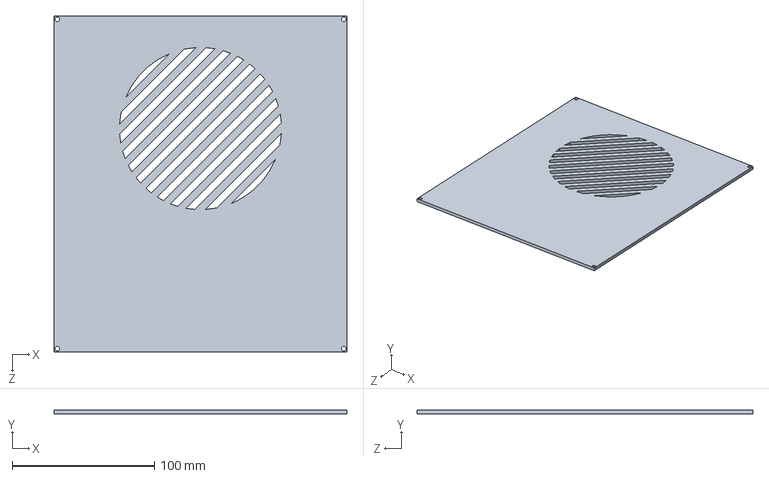
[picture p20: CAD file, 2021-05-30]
Car/3d modell/Plexiglas/roof1.SLDPRT
206.0 x 3.00 x 236.0 mm

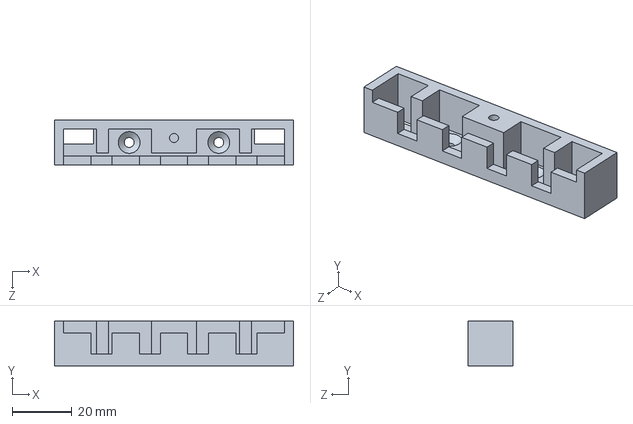
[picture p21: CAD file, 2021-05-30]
Car/3d modell/Solidworks Files/Scheinwerfer_Gehäuse.SLDPRT
80.0 x 15.0 x 15.0 mm

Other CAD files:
Car/3d modell/3dprint/base-ecke-halter-links.STL
Car/3d modell/Plexiglas/base-ecke-halter.SLDPRT
Controller/Assembly/gehaeuse_bot.STL
Car/3d modell/Plexiglas/wandhalter.SLDPRT
Car/3d modell/3dprint/LORA_mount.STL
Car/3d modell/3dprint/Scheinwerfer_Gehäuse.STL
Car/3d modell/3dprint/Scheinwerfer_deckel.STL
Car/3d modell/Solidworks Files/Vent_mount.SLDPRT
Car/3d modell/Solidworks Files/base_plate.SLDDRW

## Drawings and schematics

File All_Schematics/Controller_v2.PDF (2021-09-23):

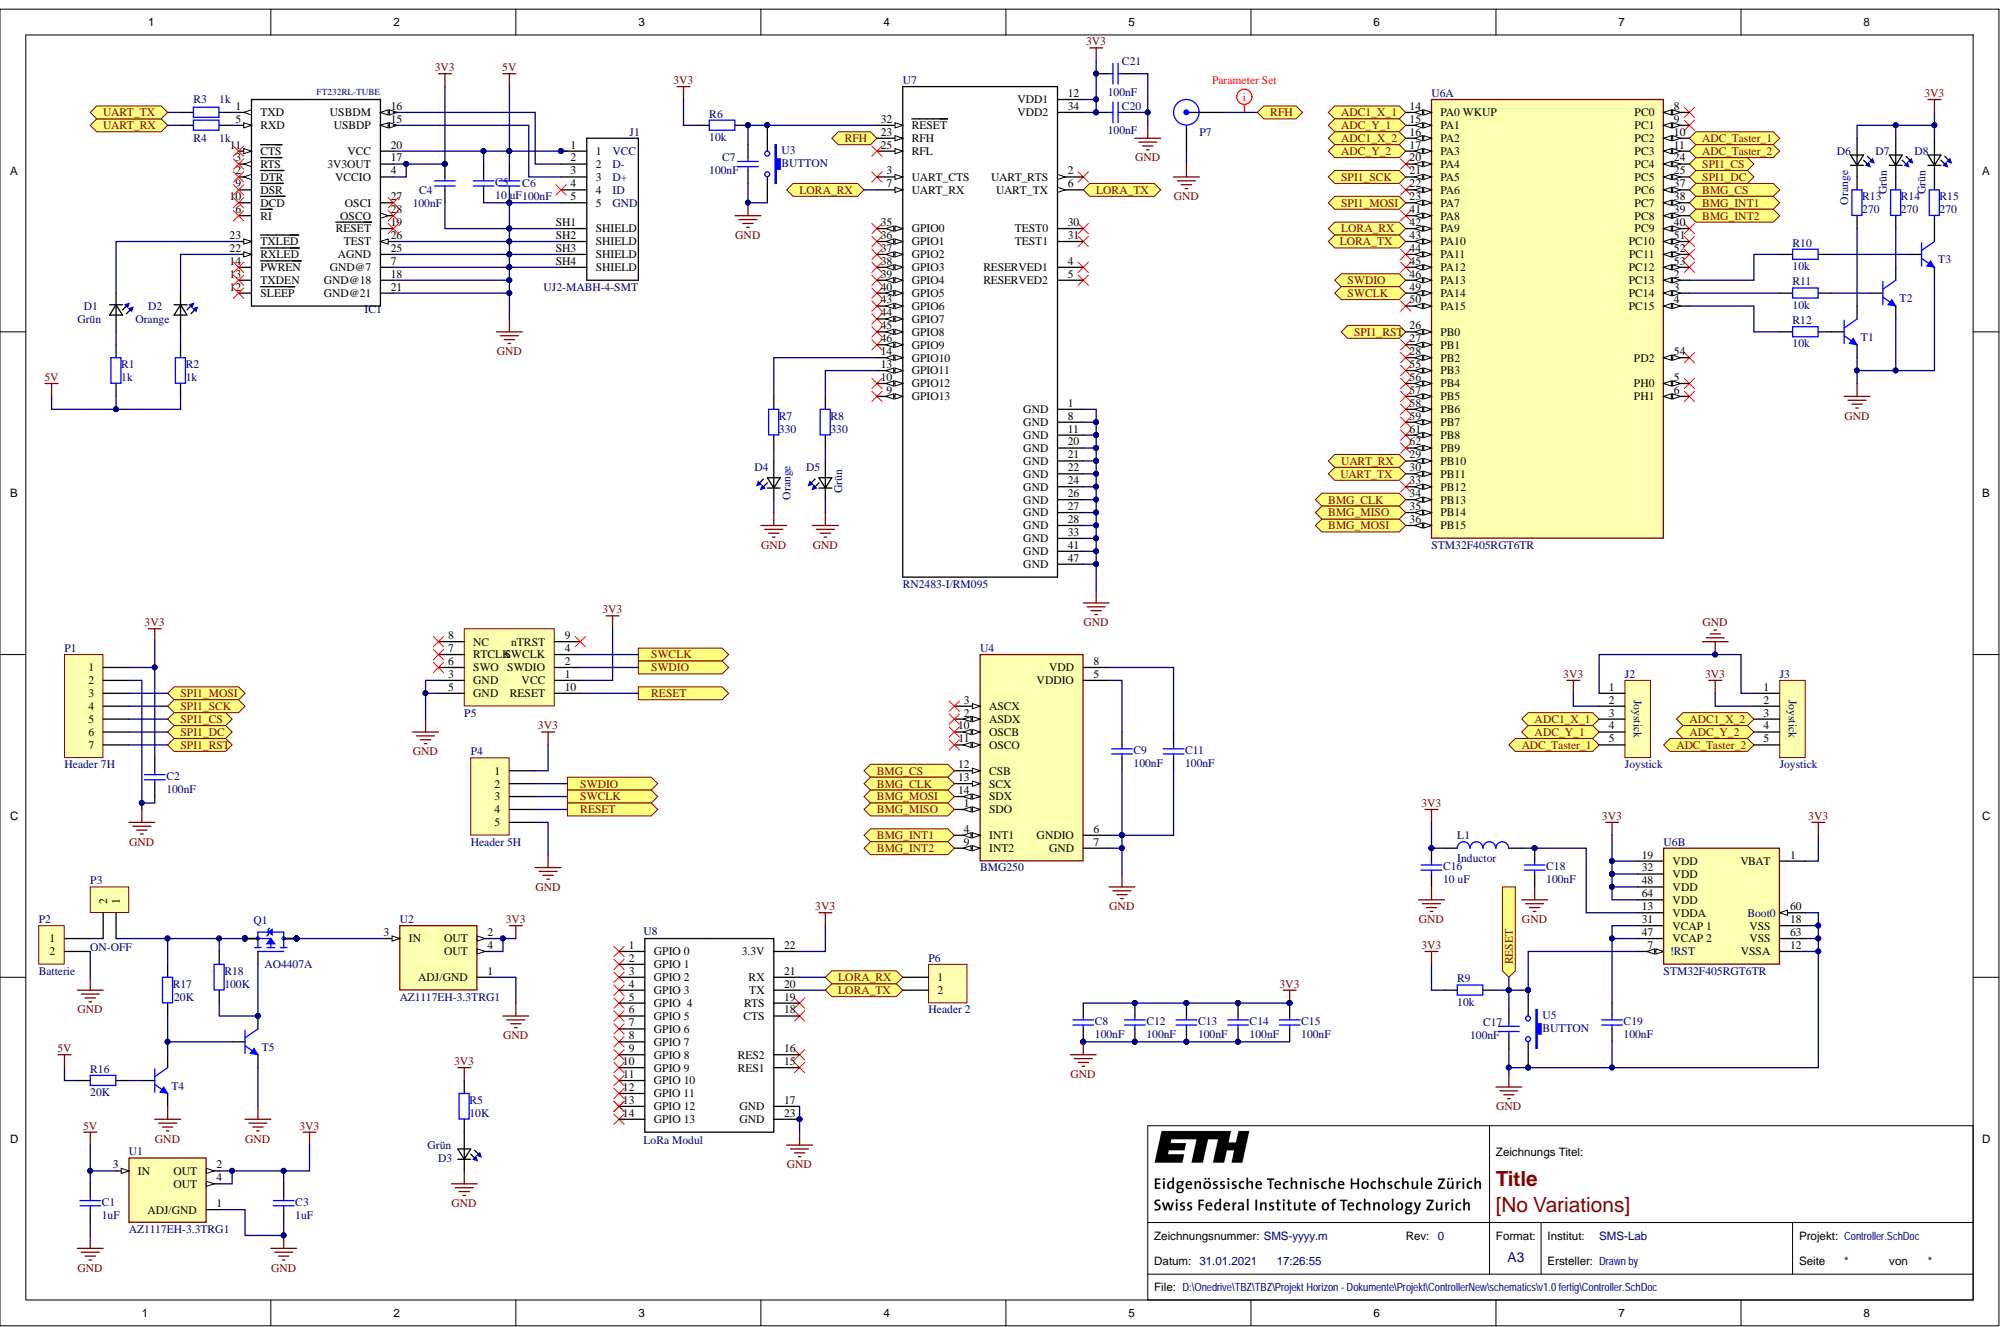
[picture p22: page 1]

File:
D:\Onedrive\TBZ\TBZ\Projekt Horizon - Dokumente\Projekt\ControllerNew\schematics\v1.0 fertig\Controller.SchDoc

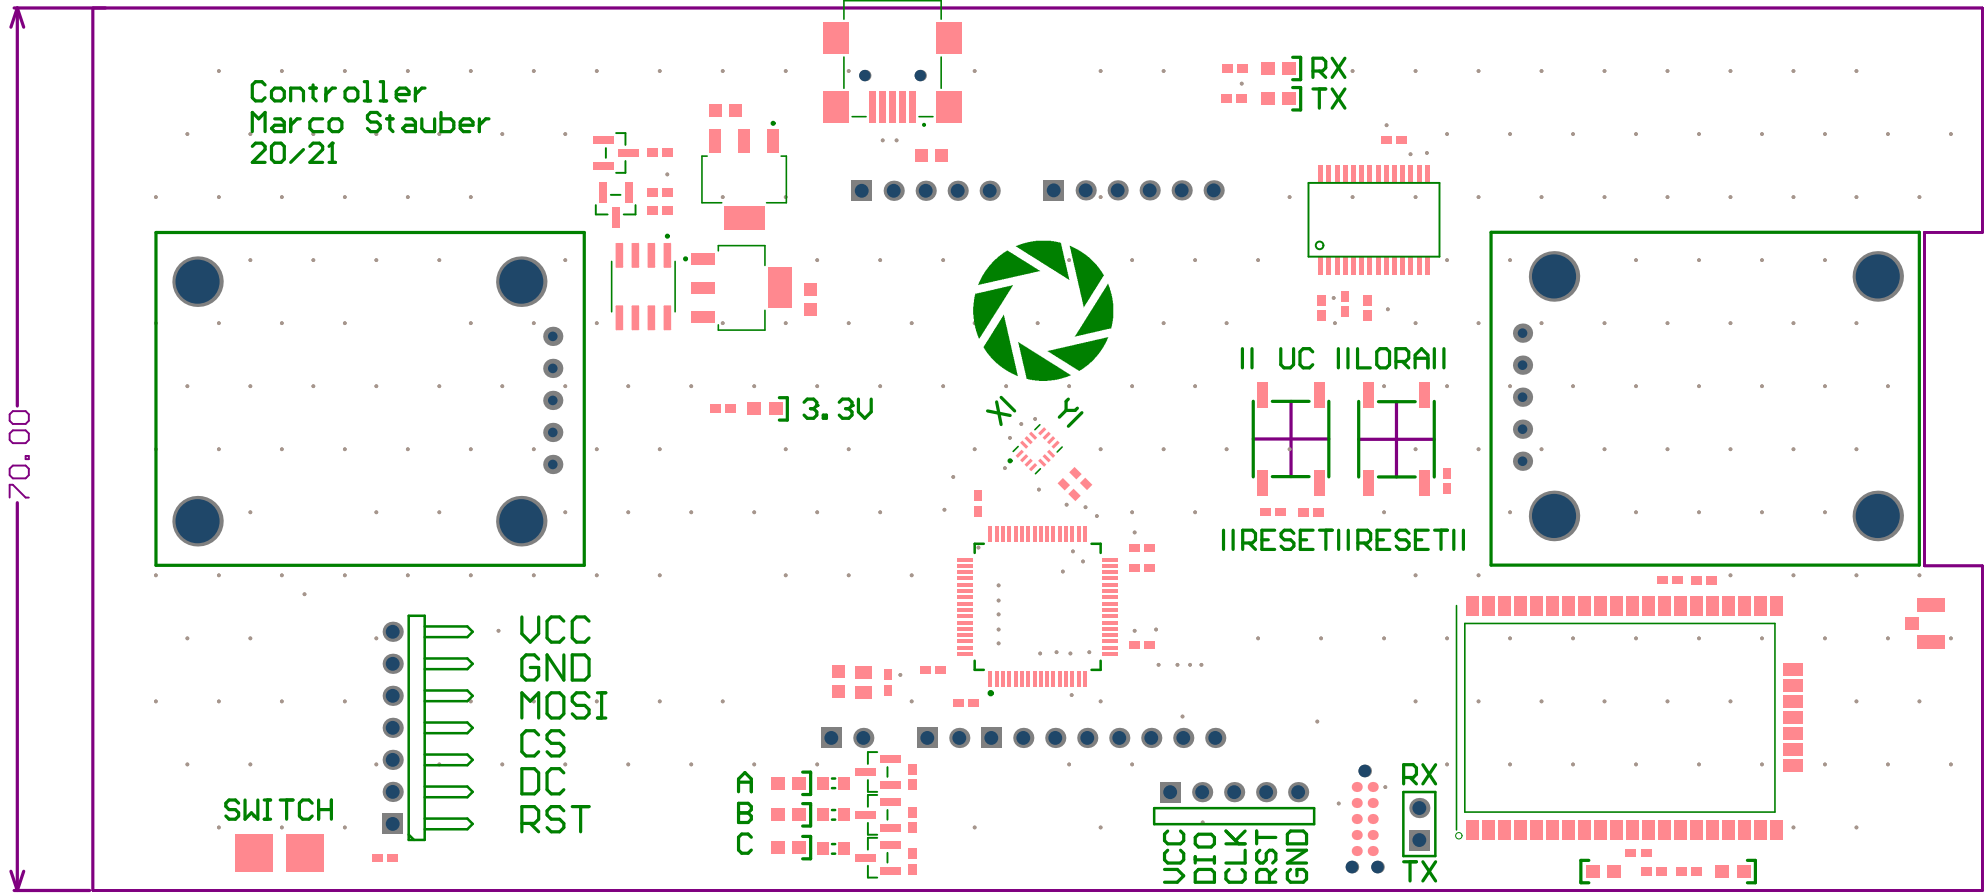
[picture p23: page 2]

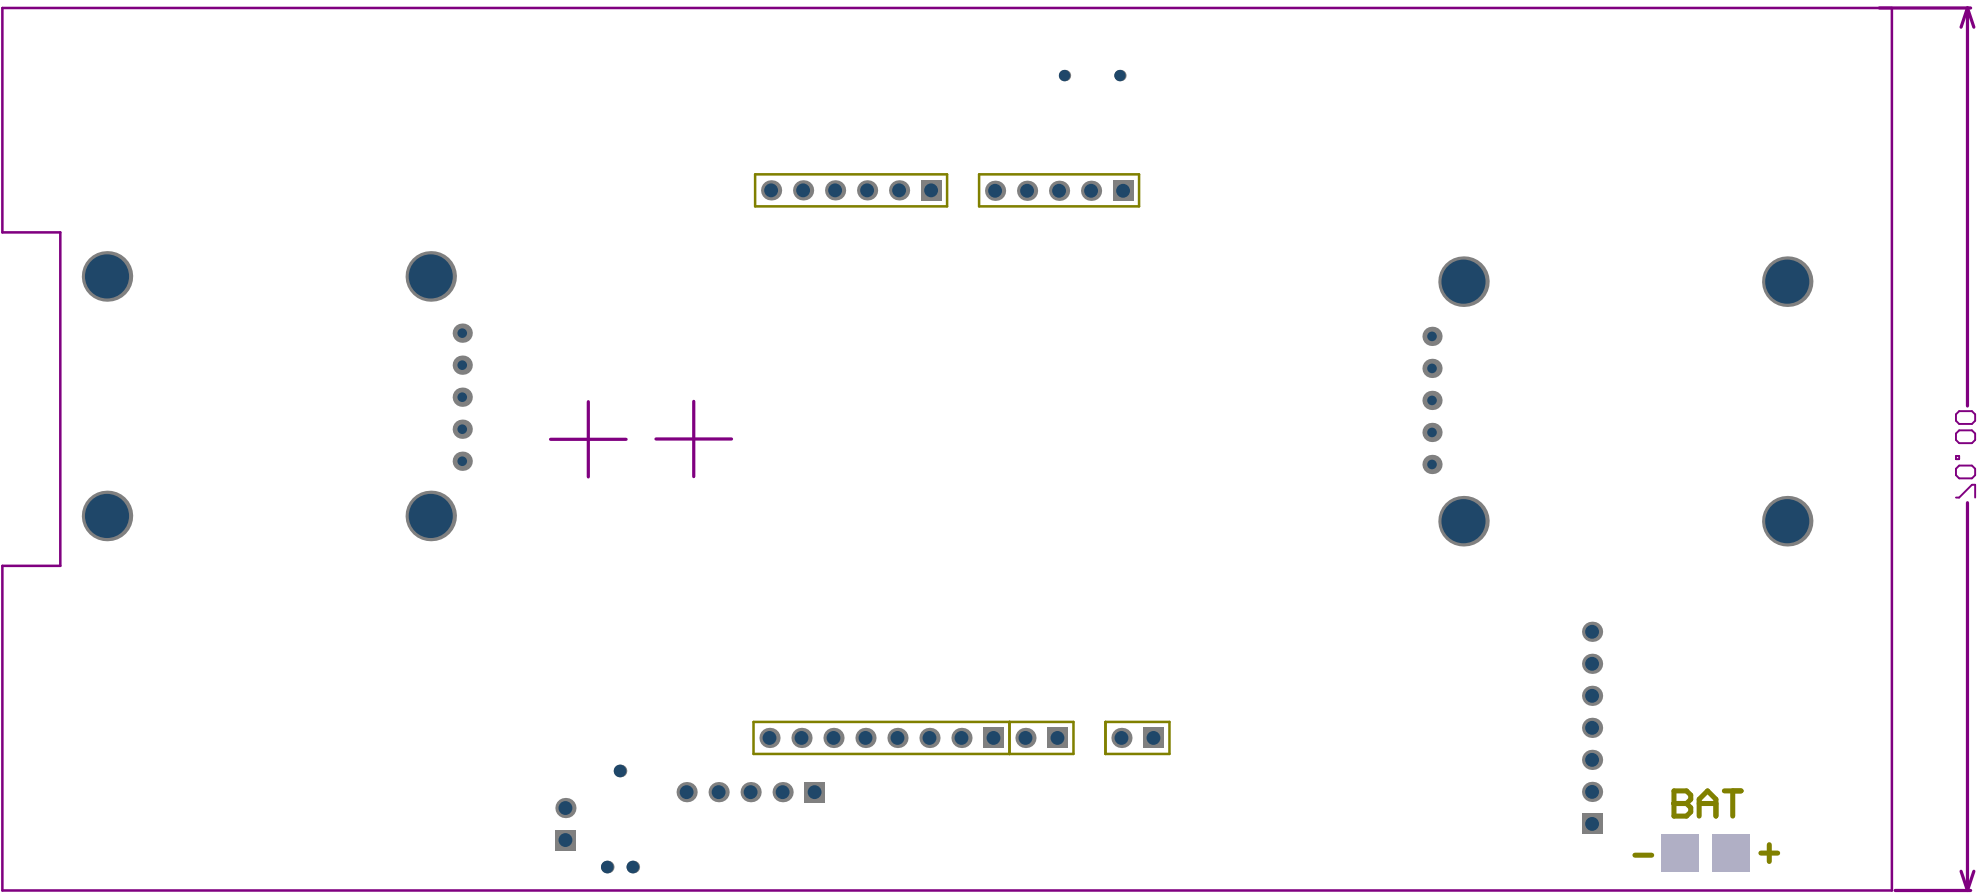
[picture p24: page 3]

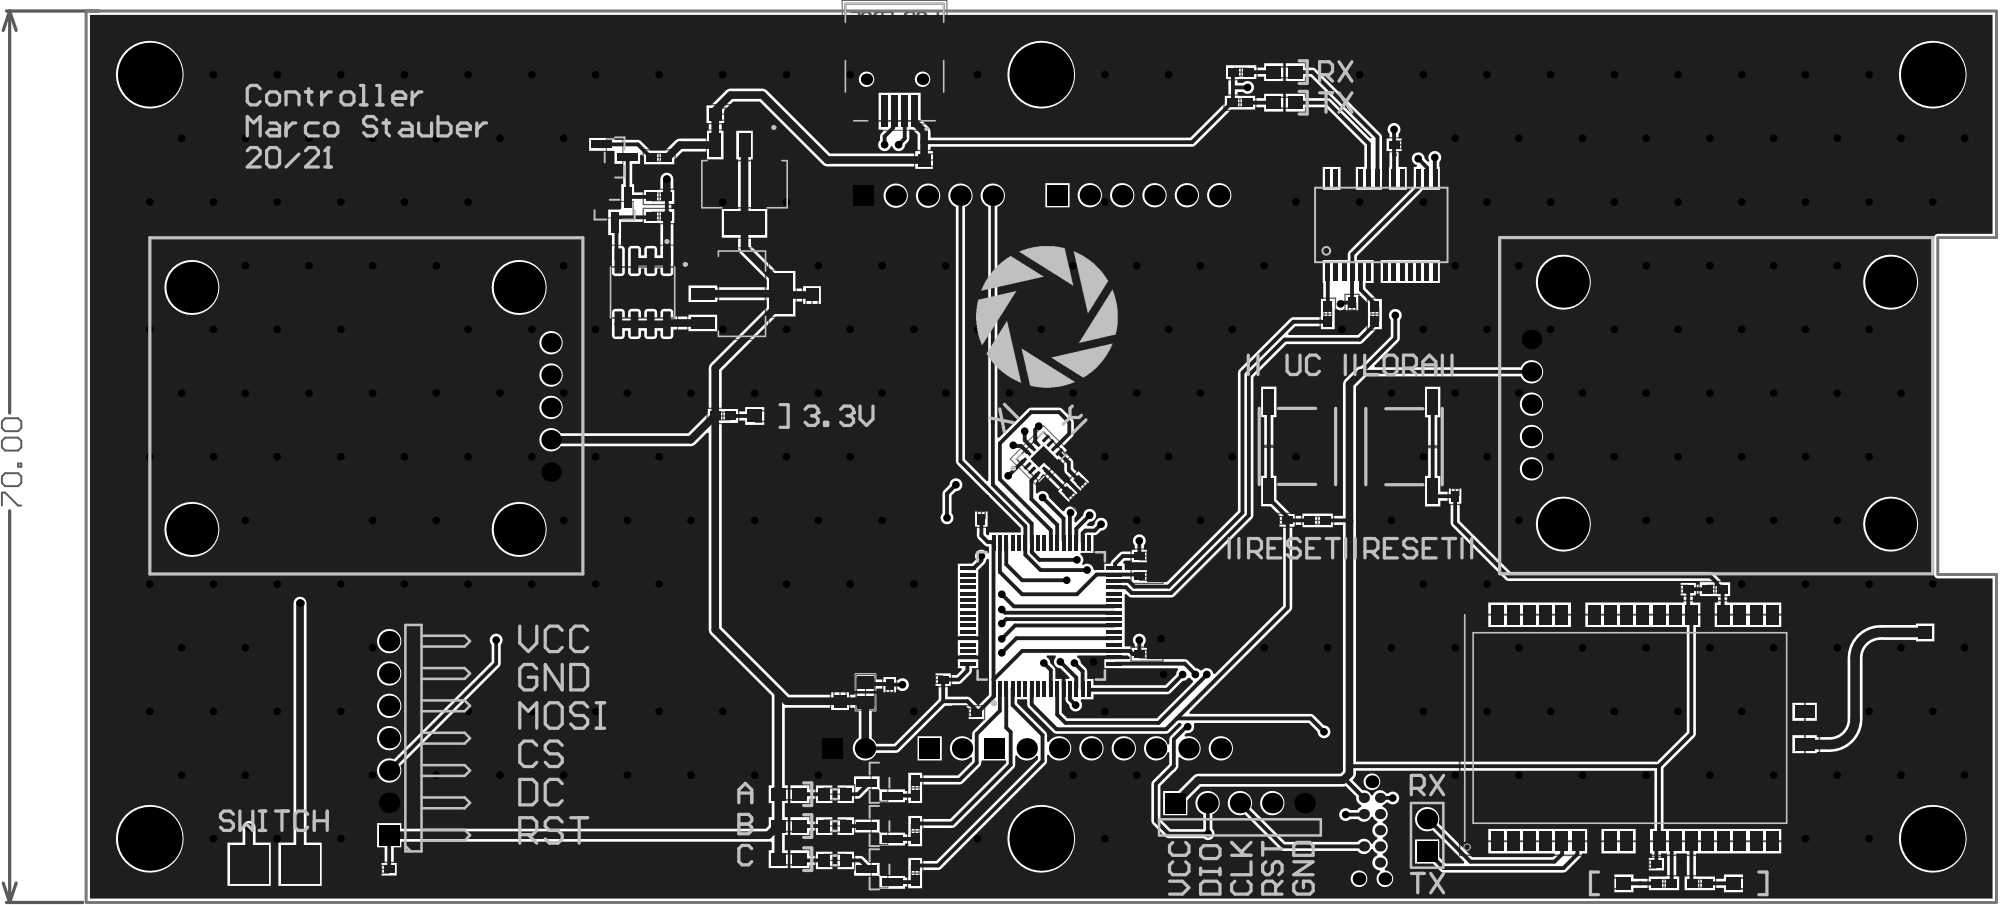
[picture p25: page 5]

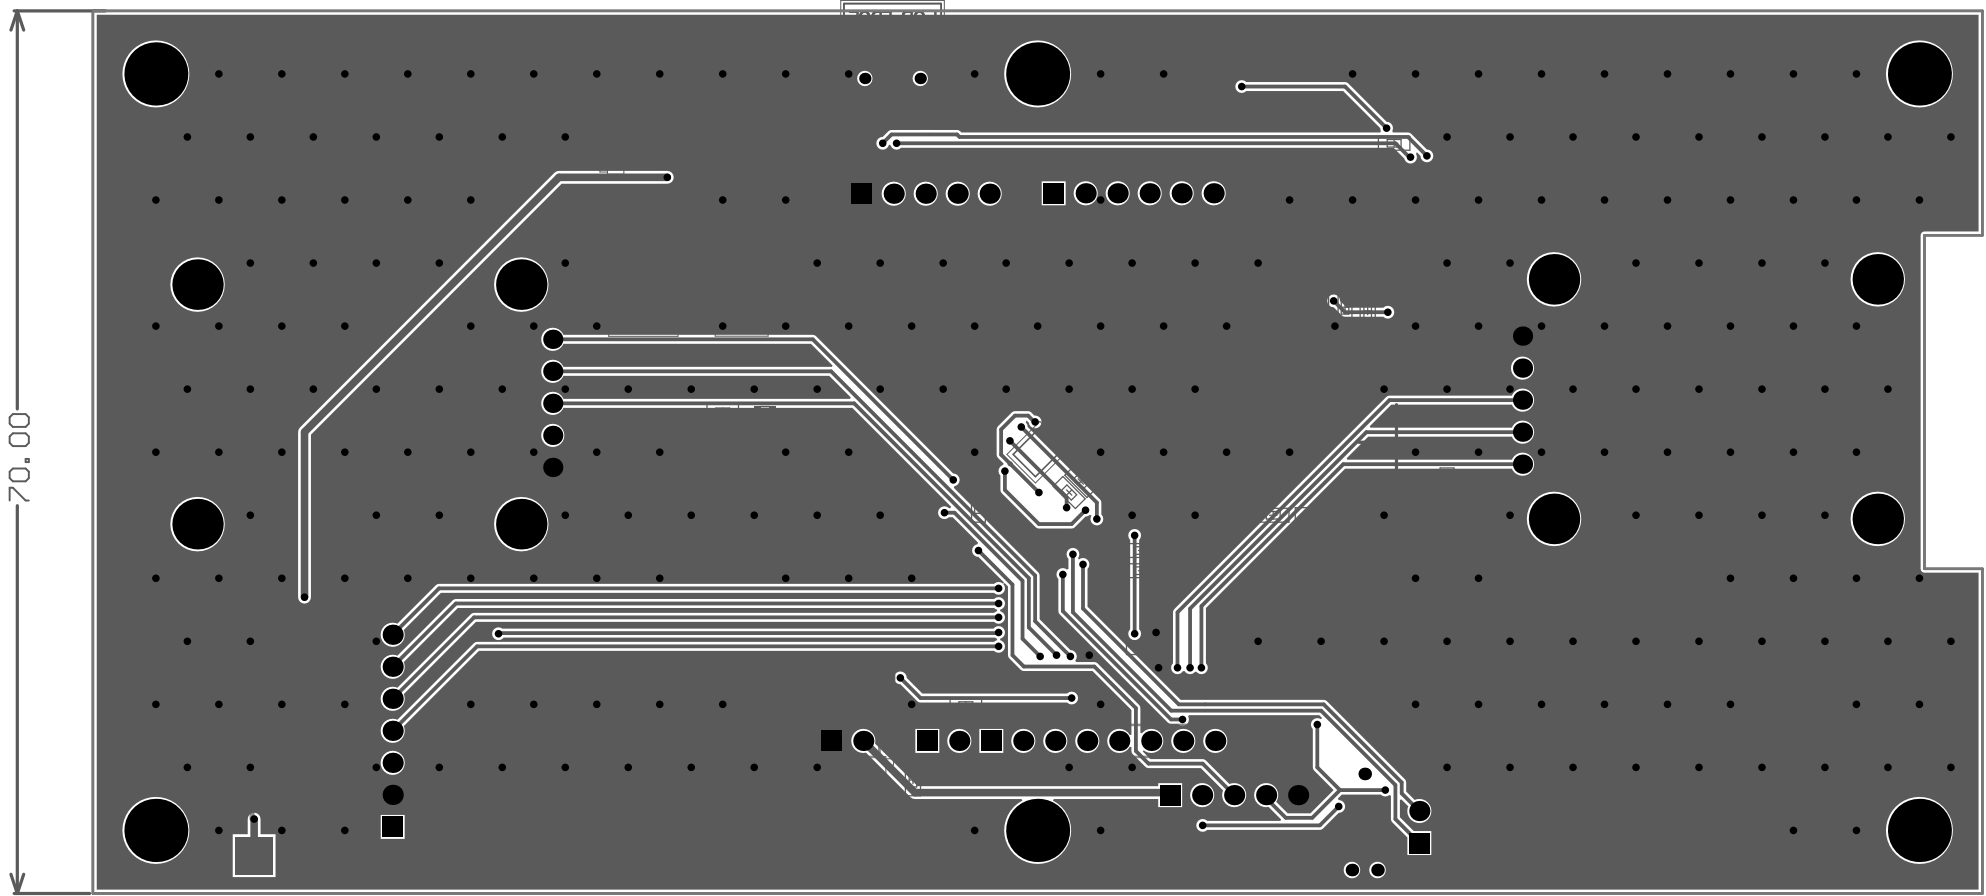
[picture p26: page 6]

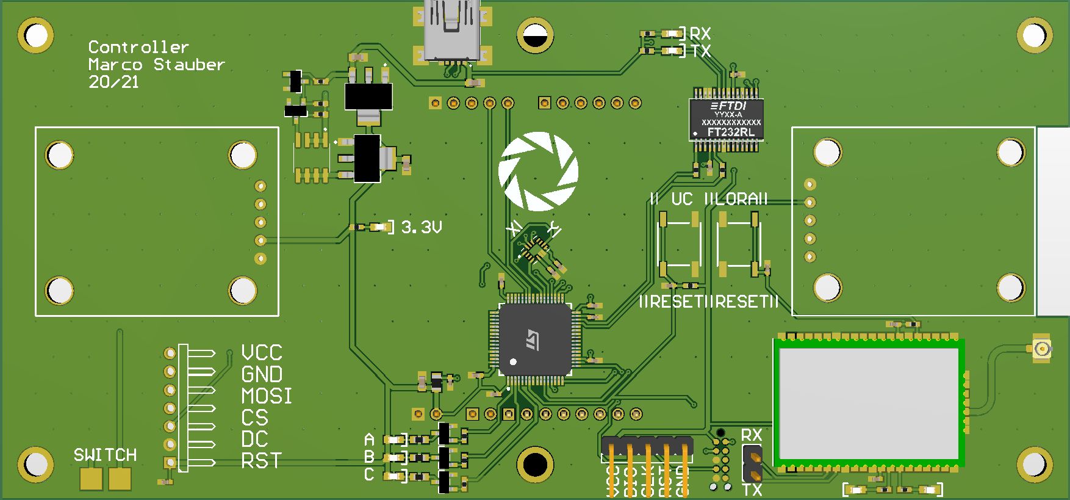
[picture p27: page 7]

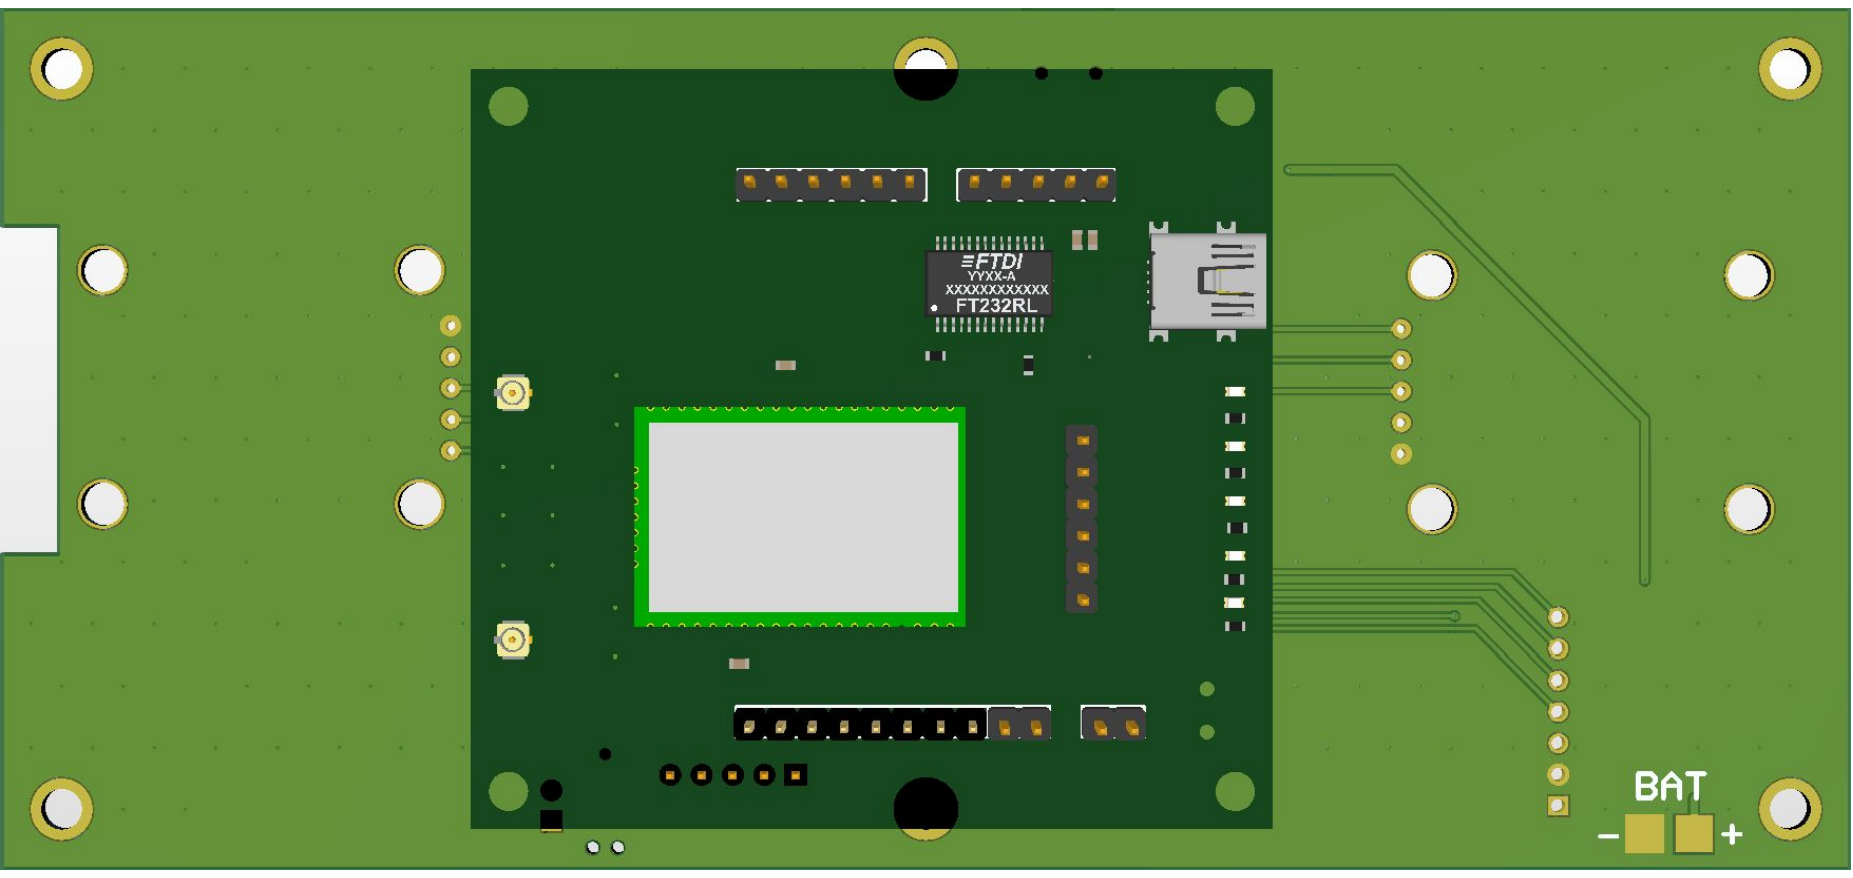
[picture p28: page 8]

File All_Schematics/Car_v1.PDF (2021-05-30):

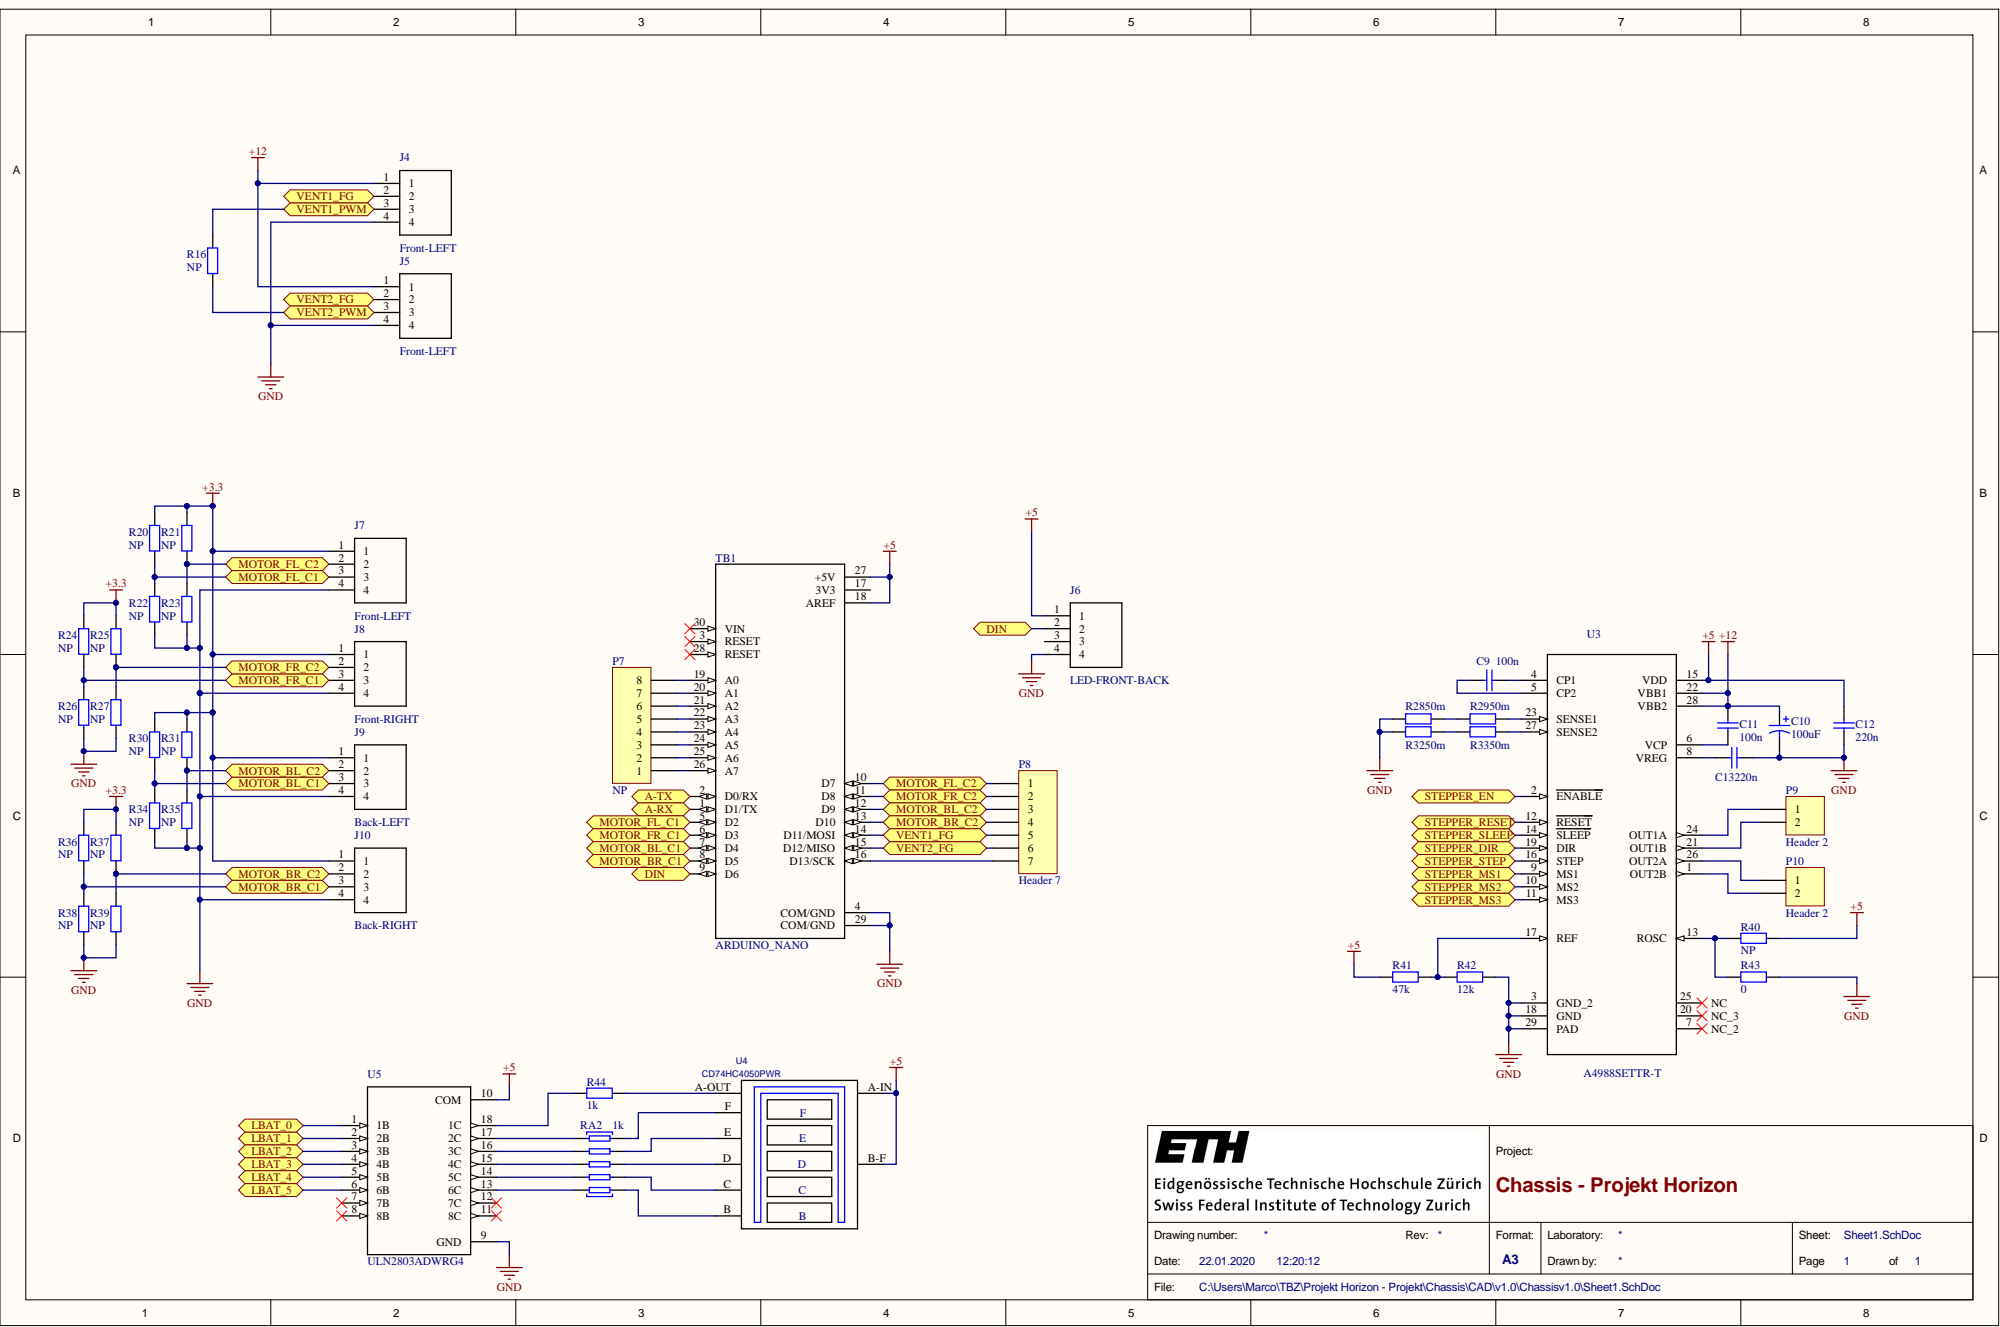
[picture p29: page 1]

C:\Users\Marco\TBZ\Projekt Horizon - Projekt\Chassis\CAD\v1.0\Chassisv1.0\Sheet1.SchDoc

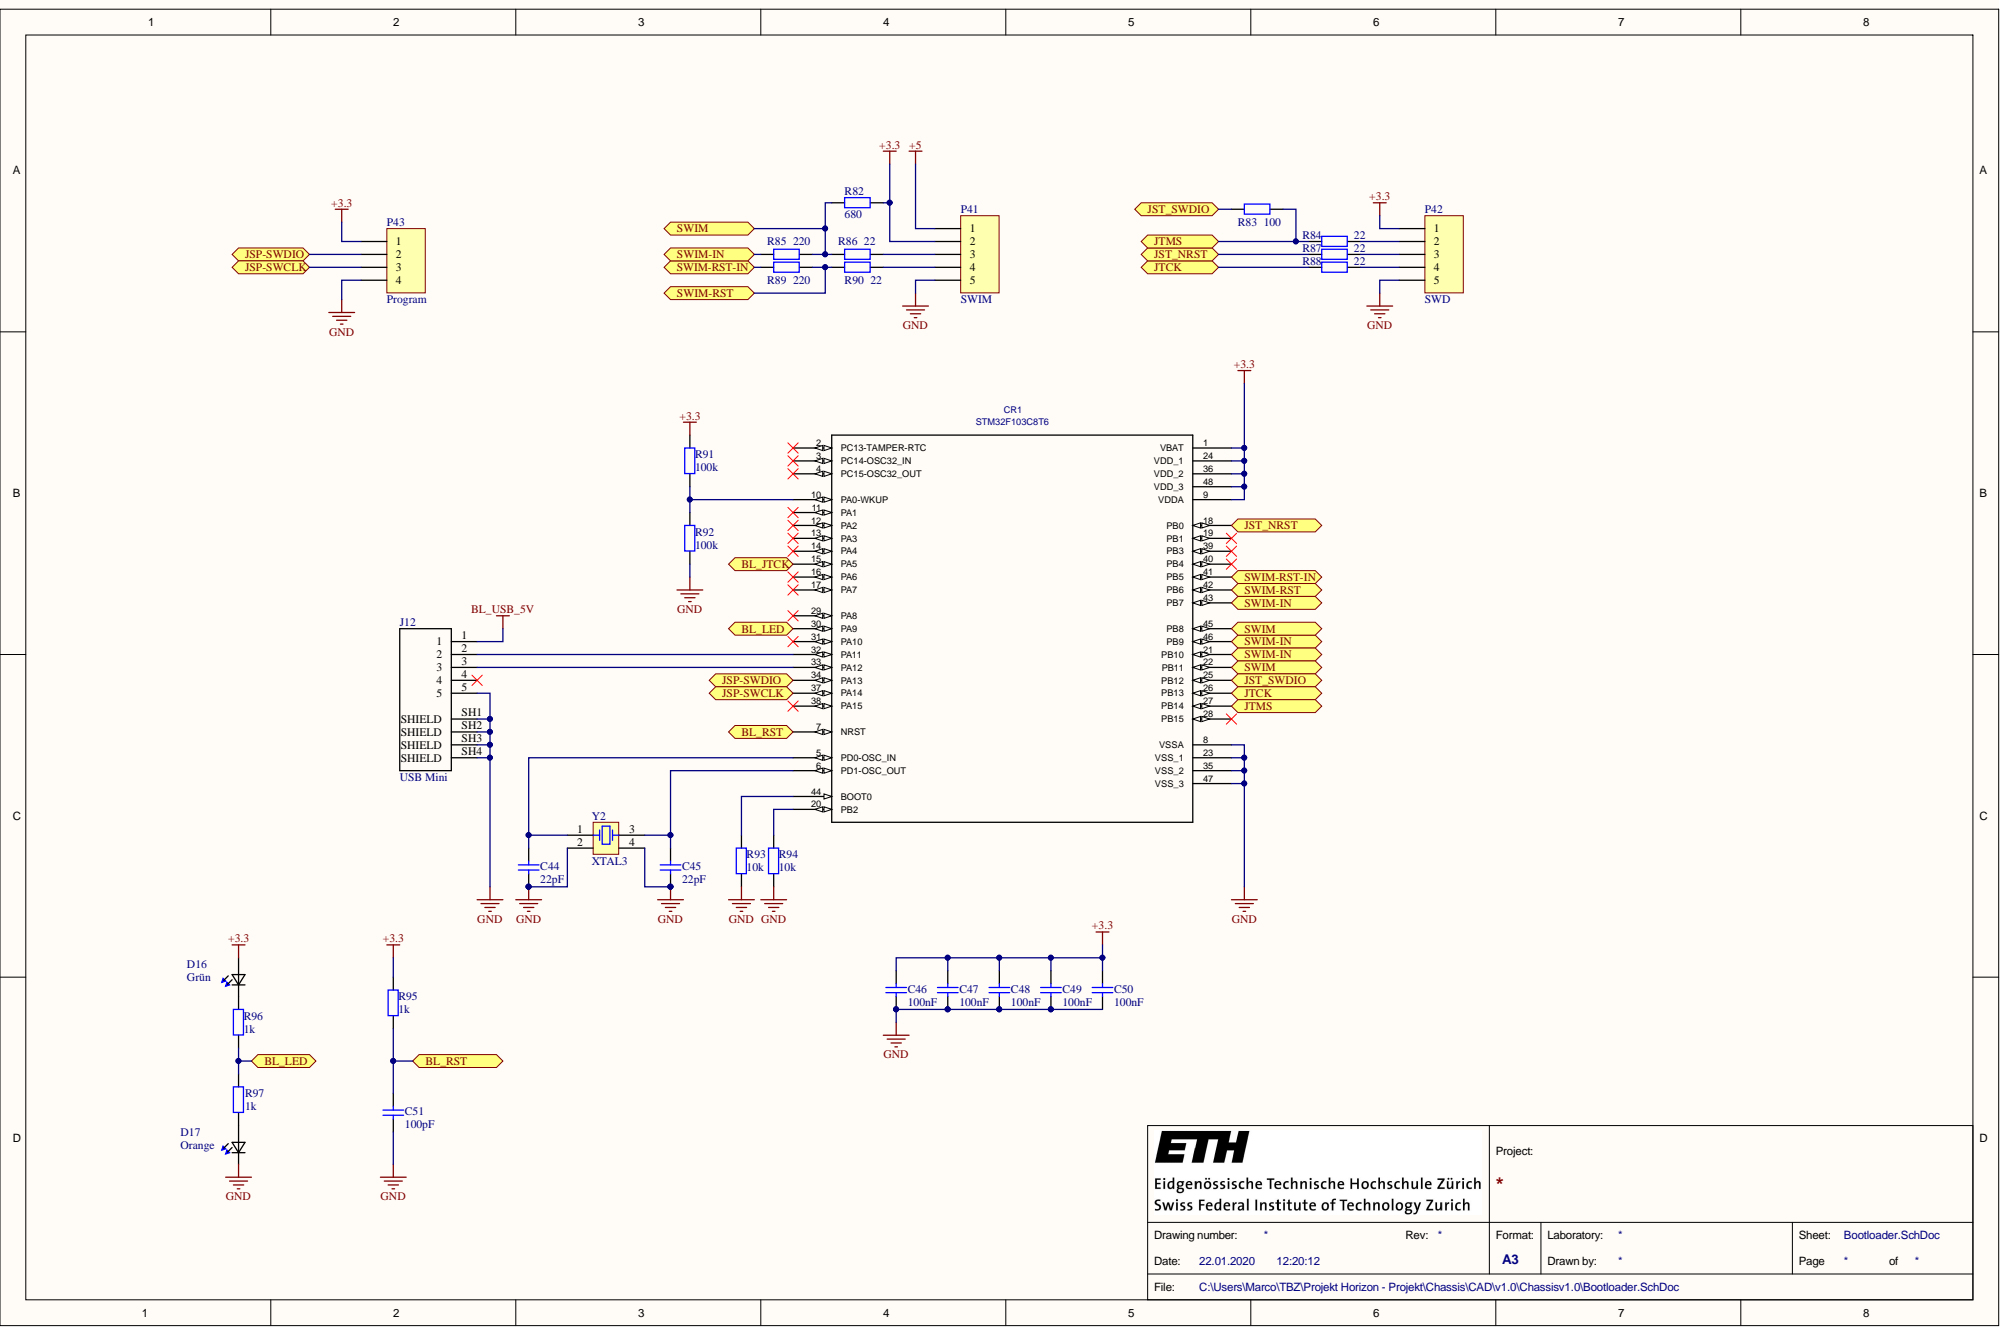
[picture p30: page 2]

BOOT0 44
PB2 20

Project: *

Drawing number: * Rev: * | Format: A3 | Laboratory: * | Sheet: Bootloader.SchDoc Page * of *

C:\Users\Marco\TBZ\Projekt Horizon - Projekt\Chassis\CAD\v1.0\Chassisv1.0\Bootloader.SchDoc

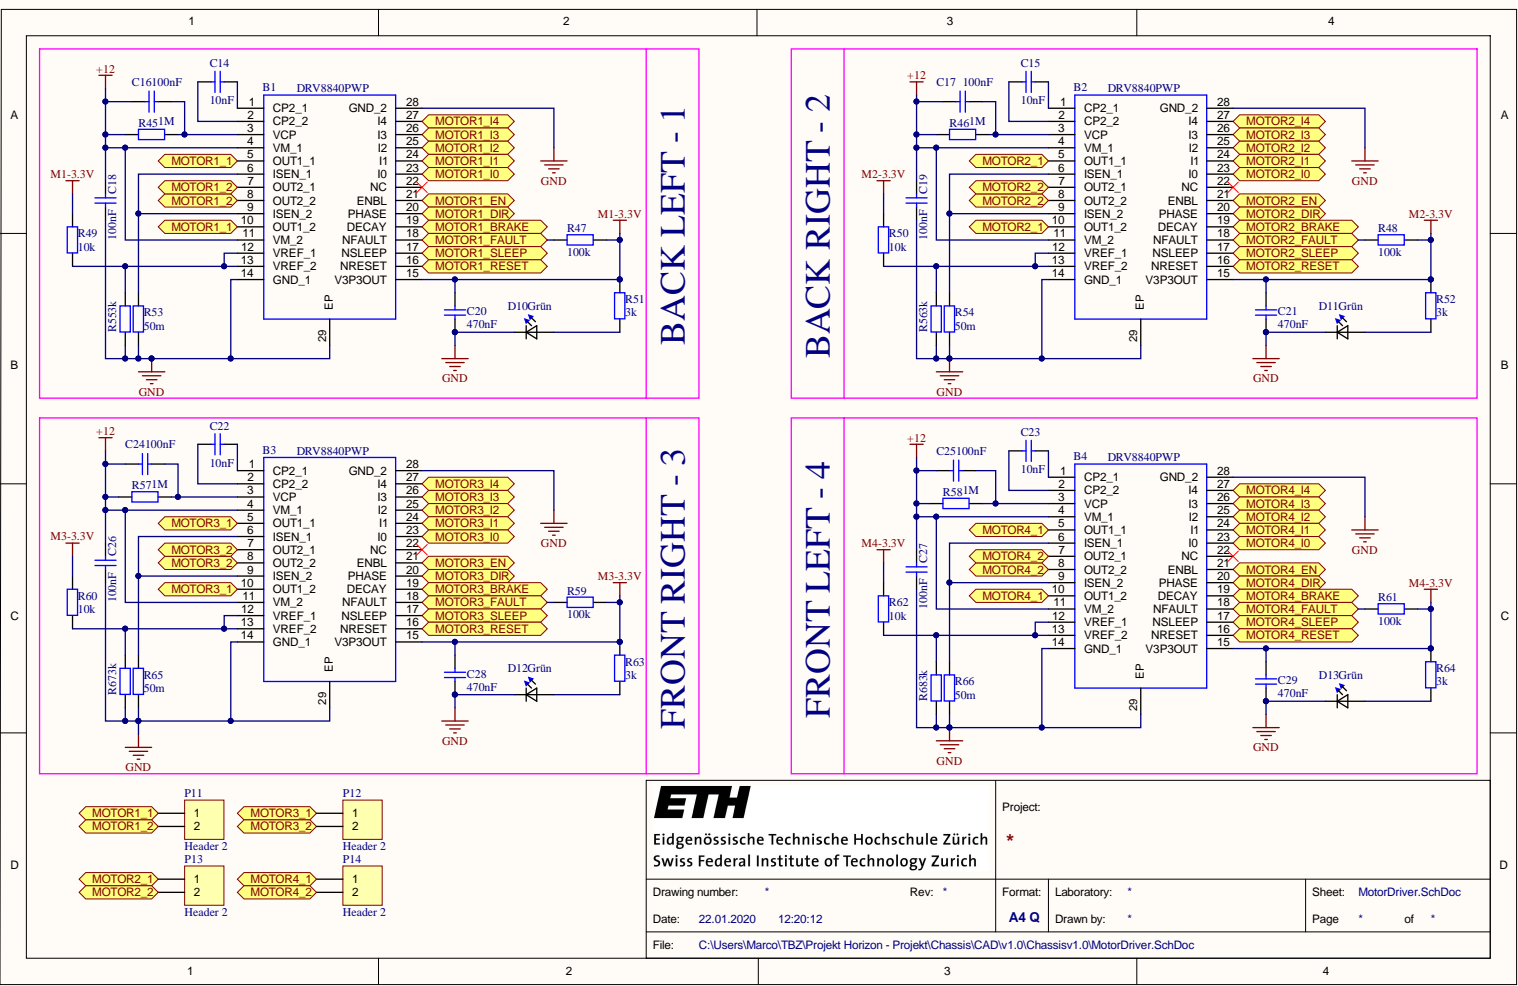
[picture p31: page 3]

MOTOR3_1 | OUT1_1 5 | MOTOR3_I0 MOTOR3_EN MOTOR3_DIR

MOTOR4_1 | OUT1_1 5 | MOTOR4_I0 MOTOR4_EN MOTOR4_DIR

Project: *

Drawing number: * Rev: * | Format: A4 Q | Laboratory: * | Sheet: MotorDriver.SchDoc

C:\Users\Marco\TBZ\Projekt Horizon - Projekt\Chassis\CAD\v1.0\Chassisv1.0\MotorDriver.SchDoc

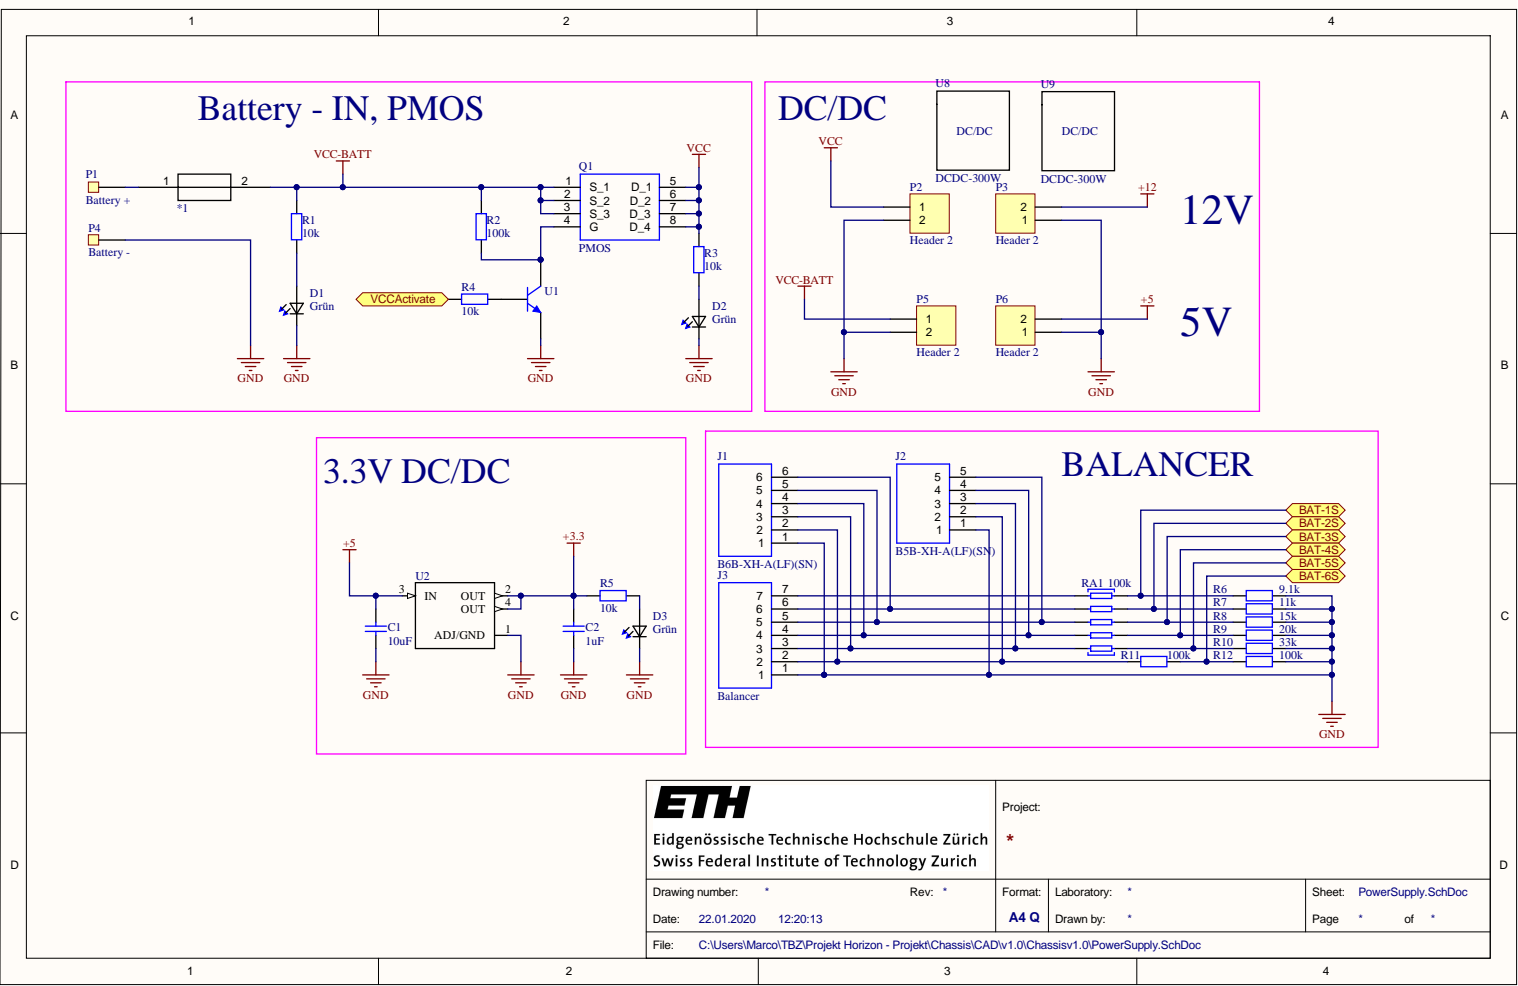
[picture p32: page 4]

R7 | 11k
R8 | 15k
R9 | 20k
R10 | 33k

Project: *

Drawing number: * Rev: * | Format: A4 Q | Laboratory: * | Sheet: PowerSupply.SchDoc

C:\Users\Marco\TBZ\Projekt Horizon - Projekt\Chassis\CAD\v1.0\Chassisv1.0\PowerSupply.SchDoc

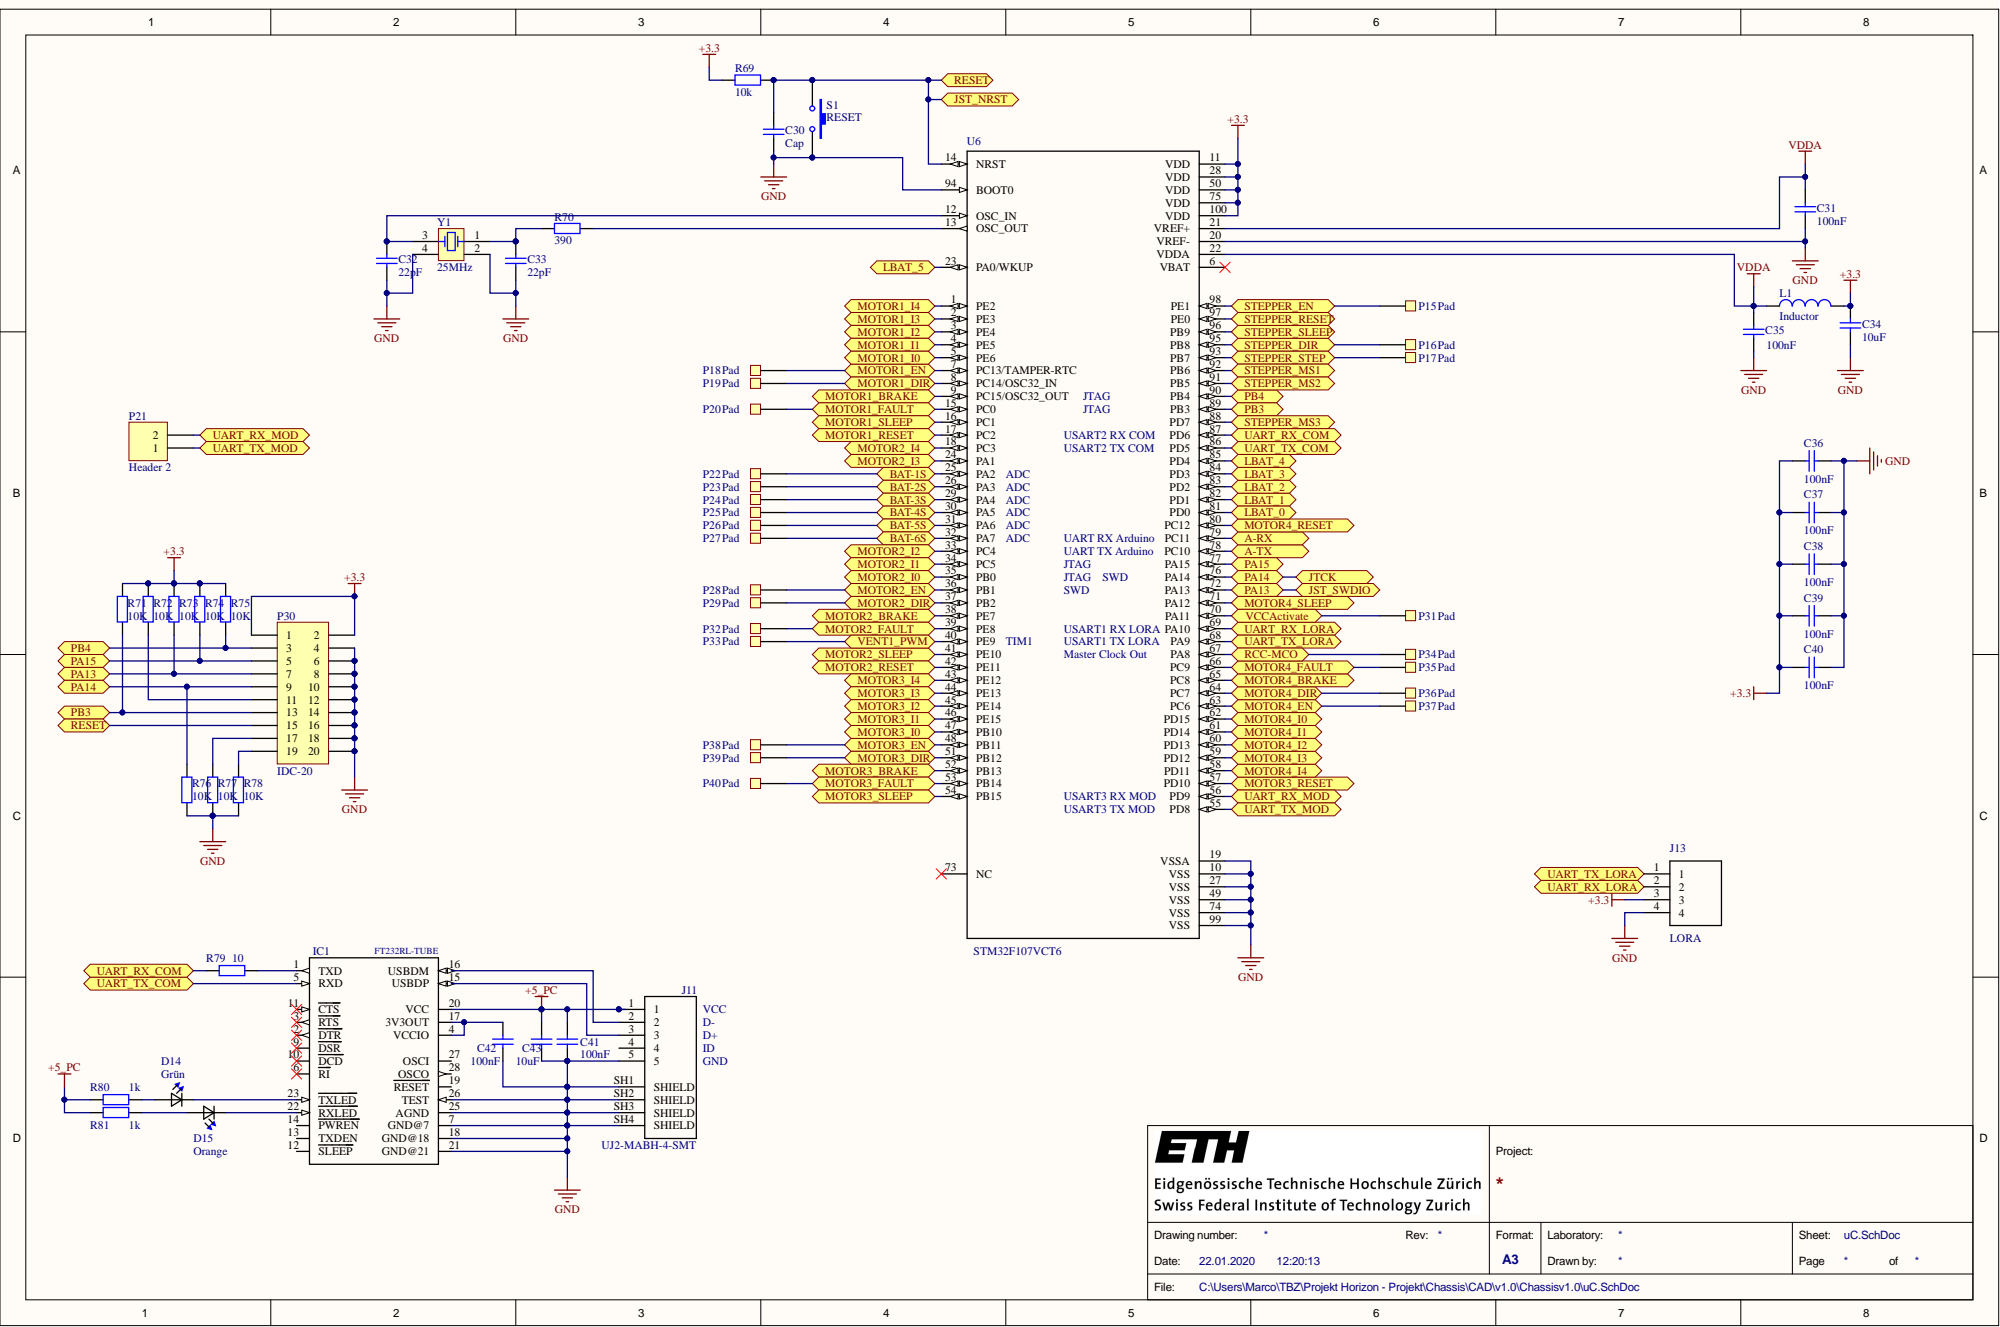
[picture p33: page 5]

Project: *

Drawing number: * Rev: * | Format: A3 | Laboratory: * | Sheet: uC.SchDoc

C:\Users\Marco\TBZ\Projekt Horizon - Projekt\Chassis\CAD\v1.0\Chassisv1.0\uC.SchDoc



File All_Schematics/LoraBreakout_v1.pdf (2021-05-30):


Projec t : LoRa Modu l

Dr awing n u mber : 1 Rev : 1 Da te: 10.10.2019 21:40:52 | For m a t : A3 | Labor ator y : Tec hSt a f f IDSC Dr aw n by : M a rco St a uber | Sheet : Fu n k .SchDoc Page 1 of 1

ve\TBZ\TBZ\Projek


# Board Stack Report

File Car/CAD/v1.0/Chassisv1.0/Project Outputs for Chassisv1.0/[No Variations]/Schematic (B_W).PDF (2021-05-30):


C:\Users\Marco\TBZ\Projekt Horizon - Projekt\Chassis\CAD\v1.0\Chassisv1.0\Sheet1.SchDoc


BOOT0 44
PB2 20

Project: *

Bootloader.SchDoc Page * of *

C:\Users\Marco\TBZ\Projekt Horizon - Projekt\Chassis\CAD\v1.0\Chassisv1.0\Bootloader.SchDoc


MOTOR3_1 | OUT1_1 5 | MOTOR3_I0 MOTOR3_EN MOTOR3_DIR

MOTOR4_1 | OUT1_1 5 | MOTOR4_I0 MOTOR4_EN MOTOR4_DIR

Project: *

Drawing number: * Rev: * | Format: A4 Q | Laboratory: * | Sheet: MotorDriver.SchDoc

C:\Users\Marco\TBZ\Projekt Horizon - Projekt\Chassis\CAD\v1.0\Chassisv1.0\MotorDriver.SchDoc


R7 | 11k
R8 | 15k
R9 | 20k
R10 | 33k

Project: *

Drawing number: * Rev: * | Format: A4 Q | Laboratory: * | Sheet: PowerSupply.SchDoc

C:\Users\Marco\TBZ\Projekt Horizon - Projekt\Chassis\CAD\v1.0\Chassisv1.0\PowerSupply.SchDoc


Project: *

uC.SchDoc

C:\Users\Marco\TBZ\Projekt Horizon - Projekt\Chassis\CAD\v1.0\Chassisv1.0\uC.SchDoc

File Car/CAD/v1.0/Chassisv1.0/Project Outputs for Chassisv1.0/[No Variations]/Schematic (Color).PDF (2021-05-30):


C:\Users\Marco\TBZ\Projekt Horizon - Projekt\Chassis\CAD\v1.0\Chassisv1.0\Sheet1.SchDoc


BOOT0 44
PB2 20

Project: *

Bootloader.SchDoc Page * of *

C:\Users\Marco\TBZ\Projekt Horizon - Projekt\Chassis\CAD\v1.0\Chassisv1.0\Bootloader.SchDoc


MOTOR3_1 | OUT1_1 5 | MOTOR3_I0 MOTOR3_EN MOTOR3_DIR

MOTOR4_1 | OUT1_1 5 | MOTOR4_I0 MOTOR4_EN MOTOR4_DIR

Project: *

Drawing number: * Rev: * | Format: A4 Q | Laboratory: * | Sheet: MotorDriver.SchDoc

C:\Users\Marco\TBZ\Projekt Horizon - Projekt\Chassis\CAD\v1.0\Chassisv1.0\MotorDriver.SchDoc


R7 | 11k
R8 | 15k
R9 | 20k
R10 | 33k

Project: *

Drawing number: * Rev: * | Format: A4 Q | Laboratory: * | Sheet: PowerSupply.SchDoc

C:\Users\Marco\TBZ\Projekt Horizon - Projekt\Chassis\CAD\v1.0\Chassisv1.0\PowerSupply.SchDoc


Project: *

uC.SchDoc

C:\Users\Marco\TBZ\Projekt Horizon - Projekt\Chassis\CAD\v1.0\Chassisv1.0\uC.SchDoc

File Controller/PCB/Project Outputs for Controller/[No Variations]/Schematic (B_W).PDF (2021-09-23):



SPI1_MOSI SPI1_SCK

SPI1_CS SPI1_DC R25 SPI1_RST

Zeichnungs Titel: Title [No Variations]

Zeichnungsnummer: SMS-yyyy.m Rev: 0 Datum: 28.12.2019 01:20:42 | Format: A3 | Institut: SMS-Lab Ersteller: Drawn by | Projekt: Controller.SchDoc Seite * von *

File:
C:\Users\larsp\Downloads\v1.0\v1.0\Controller.SchDoc

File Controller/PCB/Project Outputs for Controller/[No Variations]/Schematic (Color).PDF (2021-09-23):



SPI1_MOSI SPI1_SCK

SPI1_CS SPI1_DC R25 SPI1_RST

Zeichnungs Titel: Title [No Variations]

Zeichnungsnummer: SMS-yyyy.m Rev: 0 Datum: 28.12.2019 01:20:39 | Format: A3 | Institut: SMS-Lab Ersteller: Drawn by | Projekt: Controller.SchDoc Seite * von *

File:
C:\Users\larsp\Downloads\v1.0\v1.0\Controller.SchDoc





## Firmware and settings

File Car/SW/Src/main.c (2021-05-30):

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

/* Includes ------------------------------------------------------------------*/
#include "main.h"

/* USER CODE BEGIN Includes */
#include "bat.h"
#include "COM.h"
#include <stdio.h>
#include "motor.h"
#include "CMDHandler.h"
#include "lora.h"
/* USER CODE END Includes */

/* USER CODE BEGIN PD */

#define true 1
#define false 0
	
/* USER CODE END PD */

ADC_HandleTypeDef hadc1;
DMA_HandleTypeDef hdma_adc1;

TIM_HandleTypeDef htim1;
TIM_HandleTypeDef htim2;
TIM_HandleTypeDef htim3;

UART_HandleTypeDef huart4;
UART_HandleTypeDef huart1;
UART_HandleTypeDef huart2;
UART_HandleTypeDef huart3;

void SystemClock_Config(void);
static void MX_GPIO_Init(void);
static void MX_DMA_Init(void);
static void MX_ADC1_Init(void);
static void MX_TIM1_Init(void);
static void MX_UART4_Init(void);
static void MX_USART1_UART_Init(void);
static void MX_USART2_UART_Init(void);
static void MX_TIM2_Init(void);
static void MX_USART3_UART_Init(void);
static void MX_TIM3_Init(void);
static void MX_NVIC_Init(void);
/* USER CODE BEGIN 0 */
		//uint8_t rx_buff[1];
		char rx_ard_buff[1];
		char rx_add_buff[1];
		char rx_lora_buff[1];
		char rx_com_buff[1];
		uint32_t ADCvalues[6];
/* USER CODE END 0 */

/**
  * @brief  The application entry point.
  * @retval int
  */
int main(void)
{
  /* MCU Configuration--------------------------------------------------------*/

  /* Reset of all peripherals, Initializes the Flash interface and the Systick. */
  HAL_Init();

  /* Configure the system clock */
  SystemClock_Config();

  /* Initialize all configured peripherals */
  MX_GPIO_Init();
	MX_TIM3_Init();
  MX_DMA_Init();
  MX_ADC1_Init();
  MX_TIM1_Init();
  MX_UART4_Init();
  MX_USART1_UART_Init();
  MX_USART2_UART_Init();
  MX_TIM2_Init();
  MX_USART3_UART_Init();
  

  /* Initialize interrupts */
  MX_NVIC_Init();
  /* USER CODE BEGIN 2 */
	
	_Bool BATOKAY = false;

	//BatLED(0x3F);
	COM_TX("START\r\n");
	
	HAL_ADC_Start_DMA(&hadc1,(uint32_t *)ADCvalues, 6);
	//HAL_ADC_Start(&hadc1);
	//HAL_ADC_Start_IT(&hadc1);
	HAL_UART_Receive_IT(&huart1,(uint8_t*)rx_lora_buff,1);
	HAL_UART_Receive_IT(&huart2,(uint8_t*)rx_com_buff,1);
	HAL_UART_Receive_IT(&huart3,(uint8_t*)rx_add_buff,1);
	HAL_UART_Receive_IT(&huart4,(uint8_t*)rx_ard_buff,1);	
	HAL_TIM_Base_Start_IT(&htim3);
	
	BatLED(0x00);
	ARD_TX("P");
	char onetimeloop = 1;
	char loop = 0;
	HAL_GPIO_WritePin(GPIOA, GPIO_PIN_11, GPIO_PIN_SET);
	/*MOTOR_3_RESET(1);
	MOTOR_3_SLEEP(1);
	MOTOR_3_BRAKE(0);
	MOTOR_3_DIR(0);
	MOTOR_3_ENABLE(1);
	MOTOR_3_CURRENT(10);*/
	
  /* USER CODE END 2 */

  /* Infinite loop */
  /* USER CODE BEGIN WHILE */
	/*while(!loop)
	{
		CH_HANDLER(0, "a",2);
		if(Ardunio_Ready(0))
			{
				loop = scheinwerfer(2);
			}
	}*/
  while(1)
  {		
		if(onetimeloop)
		{
			if(Ardunio_Ready(0))
			{
				scheinwerfer(2);
			}
			
		}
		//scheinwerfer(2);

		if(SumBAT(ADCvalues))						//	Check Battery
		{															//
			BATOKAY = true;  						//
			/*
			{
				HAL_GPIO_WritePin(GPIOA, GPIO_PIN_11, GPIO_PIN_SET);
				MOTOR_STATE(1);
				MOTOR_INIT();
				onetimeloop = 0;
				//MOTOR_4_CURRENT(5);
			}
			if(MOTOR_FAULT())
			{
				
			}*/
		}															//
		else													//
		{															//
			BATOKAY = false;						//
			/*HAL_GPIO_WritePin(GPIOA, GPIO_PIN_11, GPIO_PIN_RESET);
			onetimeloop = 1;*/
		}															//
		
		
		Lora();
		LORA_HANDLER(0,"a");
		CH_HANDLER(0, "a",2);
		
		/*	
		while(!BATOKAY || Lora_RxFlag(0,4))
		{
		
		}*/
			
  }

    /* USER CODE END WHILE */

}

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
/* USER CODE BEGIN 4 */

void HAL_UART_RxCpltCallback(UART_HandleTypeDef *huart)
{
	if(huart->Instance==USART1)				//LORA
	{
		LORA_BUFFER(rx_lora_buff);
		HAL_UART_Receive_IT(&huart1,(uint8_t*)rx_lora_buff,1);
	}
	if(huart->Instance==USART2)				//COM
	{
		CH_BUFFER(rx_com_buff, 2);
		HAL_UART_Receive_IT(&huart2,(uint8_t*)rx_com_buff,1);
	}
	if(huart->Instance==USART3)				//ADDITIONAL
	{
		CH_BUFFER(rx_add_buff, 3);
		HAL_UART_Receive_IT(&huart3,(uint8_t*)rx_add_buff,1);
	}
	if(huart->Instance==UART4)				//ARDUINO
	{
		CH_BUFFER(rx_ard_buff, 4);
		HAL_UART_Receive_IT(&huart4,(uint8_t*)rx_ard_buff,1);
	}
	
	//singleChar = alpha[0];
	//CH_BUFFER(&singleChar);
}

void HAL_ADC_ConvCpltCallback( ADC_HandleTypeDef * hadc)
{
	HAL_ADC_Start_DMA(&hadc1,ADCvalues, 6);
	//HAL_ADC_Start(&hadc1);
}

void HAL_TIM_PeriodElapsedCallback(TIM_HandleTypeDef *htim)
{
	HAL_TIM_Base_Stop_IT(&htim3);
	HAL_TIM_Base_Start_IT(&htim3);
	//COM_TX("-------INT\r\n");
	//Timer_reached(1);
}

/* USER CODE END 4 */
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


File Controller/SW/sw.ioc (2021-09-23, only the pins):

Mcu.UserName=STM32F405RGTx
PA0-WKUP.Signal=ADCx_IN0
PA1.Signal=ADCx_IN1
PA10.Signal=USART1_RX
PA13.Signal=SYS_JTMS-SWDIO
PA14.Signal=SYS_JTCK-SWCLK
PA2.Signal=ADCx_IN2
PA3.Signal=ADCx_IN3
PA5.Signal=SPI1_SCK
PA6.Signal=SPI1_MISO
PA7.Signal=SPI1_MOSI
PA8.Signal=I2C3_SCL
PA9.Signal=USART1_TX
PB0.GPIO_Label=OLED_RST
PB0.Signal=GPIO_Output
PB1.GPIO_Label=LORA_RESET
PB1.Signal=GPIO_Output
PB10.Signal=USART3_TX
PB11.Signal=USART3_RX
PC13-ANTI_TAMP.GPIO_Label=LED_A
PC13-ANTI_TAMP.Signal=GPIO_Output
PC14-OSC32_IN.GPIO_Label=LED_B
PC14-OSC32_IN.Signal=GPIO_Output
PC15-OSC32_OUT.GPIO_Label=LED_C
PC15-OSC32_OUT.Signal=GPIO_Output
PC2.GPIO_Label=ADC_BUTTON_1
PC2.Signal=GPXTI2
PC3.GPIO_Label=ADC_BUTTON_2
PC3.Signal=GPXTI3
PC4.GPIO_Label=OLED_CS
PC4.Signal=GPIO_Output
PC5.GPIO_Label=OLED_DC
PC5.Signal=GPIO_Output
PC6.GPIO_Label=BMG_CS
PC6.Signal=GPIO_Output
PC7.GPIO_Label=BMG_INT1
PC7.Signal=GPIO_Output
PC8.GPIO_Label=BMG_INT2
PC8.Signal=GPIO_Output
PC9.Signal=I2C3_SDA

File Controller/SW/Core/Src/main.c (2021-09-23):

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
/* Includes ------------------------------------------------------------------*/
#include "main.h"

/* USER CODE BEGIN Includes */
#include "COM.h"
#include "CMDHandler.h"
#include "lora.h"
#include "ssd1351.h"
#include "gfx.h"
#include "screen.h"
#include "joystick.h"
/* USER CODE END Includes */

/* USER CODE BEGIN PD */
extern Colors colors;

/* USER CODE END PD */

ADC_HandleTypeDef hadc1;
DMA_HandleTypeDef hdma_adc1;

I2C_HandleTypeDef hi2c3;

SPI_HandleTypeDef hspi1;

TIM_HandleTypeDef htim6;

UART_HandleTypeDef huart1;
UART_HandleTypeDef huart3;

/* USER CODE BEGIN PV */
char rx_lora_buff[1];
char rx_com_buff[1];
uint32_t ADCvalues[4];

char s_buf[50];

//extern Colors colors;
/* USER CODE END PV */

void SystemClock_Config(void);
static void MX_GPIO_Init(void);
static void MX_DMA_Init(void);
static void MX_ADC1_Init(void);
static void MX_SPI1_Init(void);
static void MX_USART1_UART_Init(void);
static void MX_USART3_UART_Init(void);
static void MX_I2C3_Init(void);
static void MX_TIM6_Init(void);
static void MX_NVIC_Init(void);
/* USER CODE BEGIN PFP */
void pin_cs(uint8_t pinstate);
void pin_dc(uint8_t pinstate);
void pin_rs(uint8_t pinstate);
void transmit_data(uint8_t *data, uint32_t len);
void user_delay_ms(uint32_t period);

/* USER CODE END PFP */

/**
  * @brief  The application entry point.
  * @retval int
  */
int main(void)
{
  /* MCU Configuration--------------------------------------------------------*/

  /* Reset of all peripherals, Initializes the Flash interface and the Systick. */
  HAL_Init();

  /* Configure the system clock */
  SystemClock_Config();

  /* Initialize all configured peripherals */
  MX_GPIO_Init();
  MX_DMA_Init();
  MX_ADC1_Init();
  MX_SPI1_Init();
  MX_USART1_UART_Init();
  MX_USART3_UART_Init();
  MX_I2C3_Init();
  MX_TIM6_Init();

  /* Initialize interrupts */
  MX_NVIC_Init();
  /* USER CODE BEGIN 2 */
  //SCREEN
  s_ssd1351 fnptrs_main;

  	fnptrs_main.pin_cs = pin_cs;
  	fnptrs_main.pin_rs = pin_rs;
  	fnptrs_main.pin_dc = pin_dc;
  	fnptrs_main.transmit_data = transmit_data;
  	fnptrs_main.delay = user_delay_ms;

  //INTERRUPTS
  HAL_UART_Receive_IT(&huart1,(uint8_t*)rx_lora_buff,1);
  HAL_UART_Receive_IT(&huart3,(uint8_t*)rx_com_buff,1);
  HAL_ADC_Start_DMA(&hadc1,(uint32_t *)ADCvalues, 4);
  //HAL_ADC_Start(&hadc1);

  //Turn "Running" LED on
  HAL_GPIO_WritePin(LED_A_GPIO_Port,LED_A_Pin,GPIO_PIN_SET);

  //Display Init
  init_oled(1,1, &fnptrs_main);
  screen_connecting();

  //LORA Reset
  HAL_GPIO_WritePin(LORA_RESET_GPIO_Port,LORA_RESET_Pin,GPIO_PIN_SET);
  HAL_Delay(10);
  HAL_GPIO_WritePin(LORA_RESET_GPIO_Port,LORA_RESET_Pin,GPIO_PIN_RESET);
  HAL_Delay(10);
  HAL_GPIO_WritePin(LORA_RESET_GPIO_Port,LORA_RESET_Pin,GPIO_PIN_SET);
  HAL_Delay(1000);


  //Init LORA
  if(!lora_init())
  {
	//if failed turn LED_B on
	HAL_GPIO_WritePin(LED_C_GPIO_Port,LED_C_Pin,GPIO_PIN_SET);
	while(1);
  }

  HAL_Delay(200);
  //SET "running" LED on RN2483 on
  LORA_TX("sys set pindig GPIO11 1\r\n");

  HAL_Delay(100);

  screen_init();

  //LORA_TX("radio set wdt 0\r\n");
  //HAL_Delay(100);
  while(joystick_PosCheck(0,-65,2) || joystick_PosCheck(1,65,1) || joystick_PosCheck(2,-95,2))
  {
	  Joystick(ADCvalues, 0);
  }

  //screen_connecting();
  screen_menu(0,0);

  while(joystick_PosCheck(0,0,0) || joystick_PosCheck(1,0,0) || joystick_PosCheck(2,0,0) || joystick_PosCheck(3,0,0))
  {
	  Joystick(ADCvalues, 0);
  }

  HAL_TIM_Base_Start_IT(&htim6);

  /* USER CODE END 2 */

  /* Infinite loop */
  /* USER CODE BEGIN WHILE */
  while (1)
  {
	  //COM Command Handler, a can be ignored

	  LORA_HANDLER(0,"a");
	  //lora_OFF();
	  Joystick(ADCvalues, 1);
	  HAL_Delay(500);
	  //HAL_Delay(100);
    /* USER CODE END WHILE */

    /* USER CODE BEGIN 3 */
  }
  /* USER CODE END 3 */
}

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
/* USER CODE BEGIN 4 */

void HAL_GPIO_EXTI_Callback(uint16_t GPIO_Pin)
{
	static char button1 = 0, button2 = 0;

	//falling edge
	//left js button
	if(GPIO_Pin == ADC_BUTTON_1_Pin)
	{
		if(!HAL_GPIO_ReadPin(ADC_BUTTON_1_GPIO_Port, ADC_BUTTON_1_Pin))
		{
			button1 ^= 1;
		}
		screen_menu(button1, button2);
		HAL_Delay(100);
	}
	//falling edge
	//right js button
	else if(GPIO_Pin == ADC_BUTTON_2_Pin)
	{
		if(!HAL_GPIO_ReadPin(ADC_BUTTON_2_GPIO_Port, ADC_BUTTON_2_Pin))
		{
			button2 ^= 1;
		}
		screen_menu(button1, button2);
		HAL_Delay(100);
	}
}

void HAL_UART_RxCpltCallback(UART_HandleTypeDef *huart)
{
	if(huart->Instance==USART3)				//COM
	{
		//CH_BUFFER(rx_com_buff);
		//HAL_GPIO_TogglePin(LED_C_GPIO_Port,LED_C_Pin);
		HAL_UART_Receive_IT(&huart3,(uint8_t*)rx_com_buff,1);
		CH_BUFFER(rx_com_buff);
		//HAL_UART_Transmit(&huart3, (uint8_t *)rx_com_buff, strlen(rx_com_buff), 100);
	}
	if(huart->Instance==USART1)				//LORA
	{
		//LORA_BUFFER(rx_lora_buff);
		//HAL_GPIO_TogglePin(LED_C_GPIO_Port,LED_C_Pin);
		HAL_UART_Receive_IT(&huart1,(uint8_t*)rx_lora_buff,1);
		//COM_TX(rx_lora_buff);
		LORA_BUFFER(rx_lora_buff);
	}

	//singleChar = alpha[0];
	//CH_BUFFER(&singleChar);
}

void HAL_ADC_ConvCpltCallback( ADC_HandleTypeDef * hadc)
{
	//1
		//[0] = left left/right (l=4100,r=0,m=2100)
		//[1] = left up/down (d=0,u=4100,m=2060)
		//[2] = right left/right (l=0,r=4100,m=2060)
		//[3] = right up/down (d=4100,u=0,m=2000)
	//2
		//[0] = left left/right (l=4100,r=0,m=2040)
		//[1] = left up/down (d=0,u=4100,m=2040)
		//[2] = right left/right (l=0,r=4100,m=2015)
		//[3] = right up/down (d=4100,u=0,m=2000)

		/*sprintf(s_buf,"%i",ADCvalues[3]);
		COM_TX(s_buf);
		COM_TX("\r\n");*/
		//Joystick(ADCvalues);
		//COM_TX("New Values \r\n");
		HAL_ADC_Start_DMA(&hadc1,ADCvalues, 4);
		//HAL_ADC_Start(&hadc1);

}


void HAL_TIM_PeriodElapsedCallback(TIM_HandleTypeDef* htim)
{
	//COM_TX("int\r\n");
	//lora_OD();
	lora_DTS(0,0);

}

void pin_cs(uint8_t pinstate)
{
	HAL_GPIO_WritePin(OLED_CS_GPIO_Port, OLED_CS_Pin, pinstate);
}

void pin_dc(uint8_t pinstate)
{
	HAL_GPIO_WritePin(OLED_DC_GPIO_Port, OLED_DC_Pin, pinstate);
}

void pin_rs(uint8_t pinstate)
{
	HAL_GPIO_WritePin(OLED_RST_GPIO_Port, OLED_RST_Pin, pinstate);
}

void transmit_data(uint8_t *data, uint32_t len)
{
	HAL_SPI_Transmit(&hspi1, data, len, 1000);
}
void user_delay_ms(uint32_t period)
{
	HAL_Delay(period);
}


/* USER CODE END 4 */
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


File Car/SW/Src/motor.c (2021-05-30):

#include "main.h"
#include "motor.h"
#include "math.h"
#include "com.h"

////////////////////////////////////////////////////////////////////////
//Controll All
////////////////////////////////////////////////////////////////////////
	
void MOTOR_INIT(void)
{
	MOTOR_RESET(1);
	
	HAL_Delay(100);
	MOTOR_RESET(0);
	
	HAL_Delay(100);
	MOTOR_RESET(1);
	
	MOTOR_CURRENT(0);
	MOTOR_DECAY(1);
	
	MOTOR_SLEEP(1);
	
	MOTOR_ENABLE(1);
}

void MOTOR_STOP()
{
	MOTOR_CURRENT(0);
	MOTOR_RESET(0);
	MOTOR_ENABLE(0);
	MOTOR_SLEEP(0);
	
	COM_TX("Motor STOP");
}

void MOTOR_DRIVE(char FirstX, char FirstY, char SecX)
{
		/*
				1 ______ 4		 _
				 | 			|			/ \
				 | 	  	|			 |
				 | 	  	|			 |
				2|______|3
	
	DIR(0)
			1 = CK
			2 = CK
			3 = C
			4 = C
		*/
}

void MOTOR_STATE(char state)
{
	MOTOR_1_SLEEP(state);
	MOTOR_2_SLEEP(state);
	MOTOR_3_SLEEP(state);
	MOTOR_4_SLEEP(state);
	
}
void MOTOR_DECAY(uint8_t brake)
{
	MOTOR_1_BRAKE(brake);
	MOTOR_2_BRAKE(brake);
	MOTOR_3_BRAKE(brake);
	MOTOR_4_BRAKE(brake);
}
void MOTOR_CURRENT(uint8_t uCurrent)
{
	MOTOR_1_CURRENT(uCurrent);
	MOTOR_2_CURRENT(uCurrent);
	MOTOR_3_CURRENT(uCurrent);
	MOTOR_4_CURRENT(uCurrent);
}
void MOTOR_ENABLE(uint8_t enable)
{
	MOTOR_1_ENABLE(enable);
	MOTOR_2_ENABLE(enable);
	MOTOR_3_ENABLE(enable);
	MOTOR_4_ENABLE(enable);
}
void MOTOR_RESET(uint8_t reset)
{
	MOTOR_1_RESET(reset);
	MOTOR_2_RESET(reset);
	MOTOR_3_RESET(reset);
	MOTOR_4_RESET(reset);
}

void MOTOR_SLEEP(uint8_t sleep)
{
	MOTOR_1_SLEEP(sleep);
	MOTOR_2_SLEEP(sleep);
	MOTOR_3_SLEEP(sleep);
	MOTOR_4_SLEEP(sleep);
}

char MOTOR_FAULT()
{
	if(MOTOR_1_FAULT())
	{
		return 1;
	}
	if(MOTOR_1_FAULT())
	{
		return 2;
	}
	if(MOTOR_1_FAULT())
	{
		return 3;
	}
	if(MOTOR_1_FAULT())
	{
		return 4;
	}
	return 0;
}
////////////////////////////////////////////////////////////////////////
//MOTOR 1
////////////////////////////////////////////////////////////////////////

void MOTOR_1_CURRENT(uint8_t uCurrent)
{
	if(uCurrent > 100)
	{
		uCurrent = 100;
	}
	
	HAL_GPIO_WritePin(GPIOE, GPIO_PIN_2, GPIO_PIN_RESET);
	HAL_GPIO_WritePin(GPIOE, GPIO_PIN_3, GPIO_PIN_RESET);
	HAL_GPIO_WritePin(GPIOE, GPIO_PIN_4, GPIO_PIN_RESET);
	HAL_GPIO_WritePin(GPIOE, GPIO_PIN_5, GPIO_PIN_RESET);
	HAL_GPIO_WritePin(GPIOE, GPIO_PIN_6, GPIO_PIN_RESET);
	
	if(uCurrent & 0x01)
	{
		HAL_GPIO_WritePin(GPIOE, GPIO_PIN_6, GPIO_PIN_SET);
	}
	
	if(uCurrent & 0x02)
	{
		HAL_GPIO_WritePin(GPIOE, GPIO_PIN_5, GPIO_PIN_SET);
	}
	
	if(uCurrent & 0x04)
	{
		HAL_GPIO_WritePin(GPIOE, GPIO_PIN_4, GPIO_PIN_SET);
	}
	
	if(uCurrent & 0x08)
	{
		HAL_GPIO_WritePin(GPIOE, GPIO_PIN_3, GPIO_PIN_SET);
	}
	
	if(uCurrent & 0x10)
	{
		HAL_GPIO_WritePin(GPIOE, GPIO_PIN_2, GPIO_PIN_SET);
	}
}

//-------------------------------------------------

void MOTOR_1_ENABLE(uint8_t EN)
{
	if(EN)
	{
		HAL_GPIO_WritePin(GPIOC, GPIO_PIN_13, GPIO_PIN_SET);
	}
	else
	{
		HAL_GPIO_WritePin(GPIOC, GPIO_PIN_13, GPIO_PIN_RESET);
	}
}

//-------------------------------------------------

void MOTOR_1_DIR(uint8_t dir)
{
	if(dir)
	{
		HAL_GPIO_WritePin(GPIOC, GPIO_PIN_14, GPIO_PIN_SET);
	}
	else
	{
		HAL_GPIO_WritePin(GPIOC, GPIO_PIN_14, GPIO_PIN_RESET);
	}
}

//-------------------------------------------------

void MOTOR_1_BRAKE(uint8_t brake)
{
	if(brake)
	{
		HAL_GPIO_WritePin(GPIOC, GPIO_PIN_15, GPIO_PIN_SET);
	}
	else
	{
		HAL_GPIO_WritePin(GPIOC, GPIO_PIN_15, GPIO_PIN_RESET);
	}
}

//-------------------------------------------------

void MOTOR_1_SLEEP(uint8_t sleep)
{
	if(sleep)
	{
		HAL_GPIO_WritePin(GPIOC, GPIO_PIN_1, GPIO_PIN_SET);
	}
	else
	{
		HAL_GPIO_WritePin(GPIOC, GPIO_PIN_1, GPIO_PIN_RESET);
	}
}

//-------------------------------------------------

void MOTOR_1_RESET(uint8_t reset)
{
	if(reset)
	{
		HAL_GPIO_WritePin(GPIOC, GPIO_PIN_2, GPIO_PIN_SET);
	}
	else
	{
		HAL_GPIO_WritePin(GPIOC, GPIO_PIN_2, GPIO_PIN_RESET);
	}
}

//-------------------------------------------------

uint8_t MOTOR_1_FAULT(void)
{
	uint8_t temp = HAL_GPIO_ReadPin(GPIOC, 0);
	return temp;
}

////////////////////////////////////////////////////////////////////////
//MOTOR 2
////////////////////////////////////////////////////////////////////////

void MOTOR_2_CURRENT(uint8_t uCurrent)
{
	if(uCurrent > 100)
	{
		uCurrent = 100;
	}
	
	HAL_GPIO_WritePin(GPIOB, GPIO_PIN_0, GPIO_PIN_RESET);
	HAL_GPIO_WritePin(GPIOC, GPIO_PIN_5, GPIO_PIN_RESET);
	HAL_GPIO_WritePin(GPIOC, GPIO_PIN_4, GPIO_PIN_RESET);
	HAL_GPIO_WritePin(GPIOA, GPIO_PIN_1, GPIO_PIN_RESET);
	HAL_GPIO_WritePin(GPIOC, GPIO_PIN_3, GPIO_PIN_RESET);
	
	if(uCurrent & 0x01)
	{
		HAL_GPIO_WritePin(GPIOB, GPIO_PIN_0, GPIO_PIN_SET);
	}
	
	if(uCurrent & 0x02)
	{
		HAL_GPIO_WritePin(GPIOC, GPIO_PIN_5, GPIO_PIN_SET);
	}
	
	if(uCurrent & 0x04)
	{
		HAL_GPIO_WritePin(GPIOC, GPIO_PIN_4, GPIO_PIN_SET);
	}
	
	if(uCurrent & 0x08)
	{
		HAL_GPIO_WritePin(GPIOA, GPIO_PIN_1, GPIO_PIN_SET);
	}
	
	if(uCurrent & 0x10)
	{
		HAL_GPIO_WritePin(GPIOC, GPIO_PIN_3, GPIO_PIN_SET);
	}
}

//-------------------------------------------------

void MOTOR_2_ENABLE(uint8_t EN)
{
	if(EN)
	{
		HAL_GPIO_WritePin(GPIOB, GPIO_PIN_1, GPIO_PIN_SET);
	}
	else
	{
		HAL_GPIO_WritePin(GPIOB, GPIO_PIN_1, GPIO_PIN_RESET);
	}
}

//-------------------------------------------------

void MOTOR_2_DIR(uint8_t dir)
{
	if(dir)
	{
		HAL_GPIO_WritePin(GPIOB, GPIO_PIN_2, GPIO_PIN_SET);
	}
	else
	{
		HAL_GPIO_WritePin(GPIOB, GPIO_PIN_2, GPIO_PIN_RESET);
	}
}

//-------------------------------------------------

void MOTOR_2_BRAKE(uint8_t brake)
{
	if(brake)
	{
		HAL_GPIO_WritePin(GPIOE, GPIO_PIN_7, GPIO_PIN_SET);
	}
	else
	{
		HAL_GPIO_WritePin(GPIOE, GPIO_PIN_7, GPIO_PIN_RESET);
	}
}

//-------------------------------------------------

void MOTOR_2_SLEEP(uint8_t sleep)
{
	if(sleep)
	{
		HAL_GPIO_WritePin(GPIOE, GPIO_PIN_10, GPIO_PIN_SET);
	}
	else
	{
		HAL_GPIO_WritePin(GPIOE, GPIO_PIN_10, GPIO_PIN_RESET);
	}
}

//-------------------------------------------------

void MOTOR_2_RESET(uint8_t reset)
{
	if(reset)
	{
		HAL_GPIO_WritePin(GPIOE, GPIO_PIN_11, GPIO_PIN_SET);
	}
	else
	{
		HAL_GPIO_WritePin(GPIOC, GPIO_PIN_2, GPIO_PIN_RESET);
	}
}

//-------------------------------------------------

uint8_t MOTOR_2_FAULT(void)
{
	uint8_t temp = HAL_GPIO_ReadPin(GPIOE, 8);
	return temp;
}

////////////////////////////////////////////////////////////////////////
//MOTOR 3
////////////////////////////////////////////////////////////////////////
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

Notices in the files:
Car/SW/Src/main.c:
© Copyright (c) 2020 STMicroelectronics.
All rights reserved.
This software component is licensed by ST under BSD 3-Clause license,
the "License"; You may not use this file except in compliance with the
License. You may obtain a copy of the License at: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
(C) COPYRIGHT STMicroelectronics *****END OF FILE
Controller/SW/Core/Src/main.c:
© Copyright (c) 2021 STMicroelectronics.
